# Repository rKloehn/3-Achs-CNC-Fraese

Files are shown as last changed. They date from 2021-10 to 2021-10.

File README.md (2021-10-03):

# 3-Achs-CNC-Fraese

Selfmade CNC-Mill for Aluminum, Wood and Steel milling

## Overview
To mill wood, aluminum and steel for future project, the desicion was made to design, construct a DIY-CNC mill. The basic concept is based upon an typical portal style cnc-mill, which is quite common in the diy world. To better stabilise and actualy mill aluminum and steel, the cnc is made out of steel beams. The mill has an work area of X500, Y700, Z150 milimeters. To drive the axis three iHSV57 servomotors with 180W each are used. The axes are guided by linear guides and driven by three ball screws. At the end of each axis there is a limit switch that can detect the end position. To control the axis, a MESA 7i76E is used, which is connected to an Intel NUC with an Ethernet cable. All three motors have a 36V power supply with max. 8.9 Ampere. The MESA card is operated with a 24V power supply. The control is done by Linux CNC.

## Work Progress
## 1. Create CAD Model 
A CAD model was created in Solidworks. Here, different concepts were first considered. In the end, I decided in favor of the steel body construction.
<p align="center">
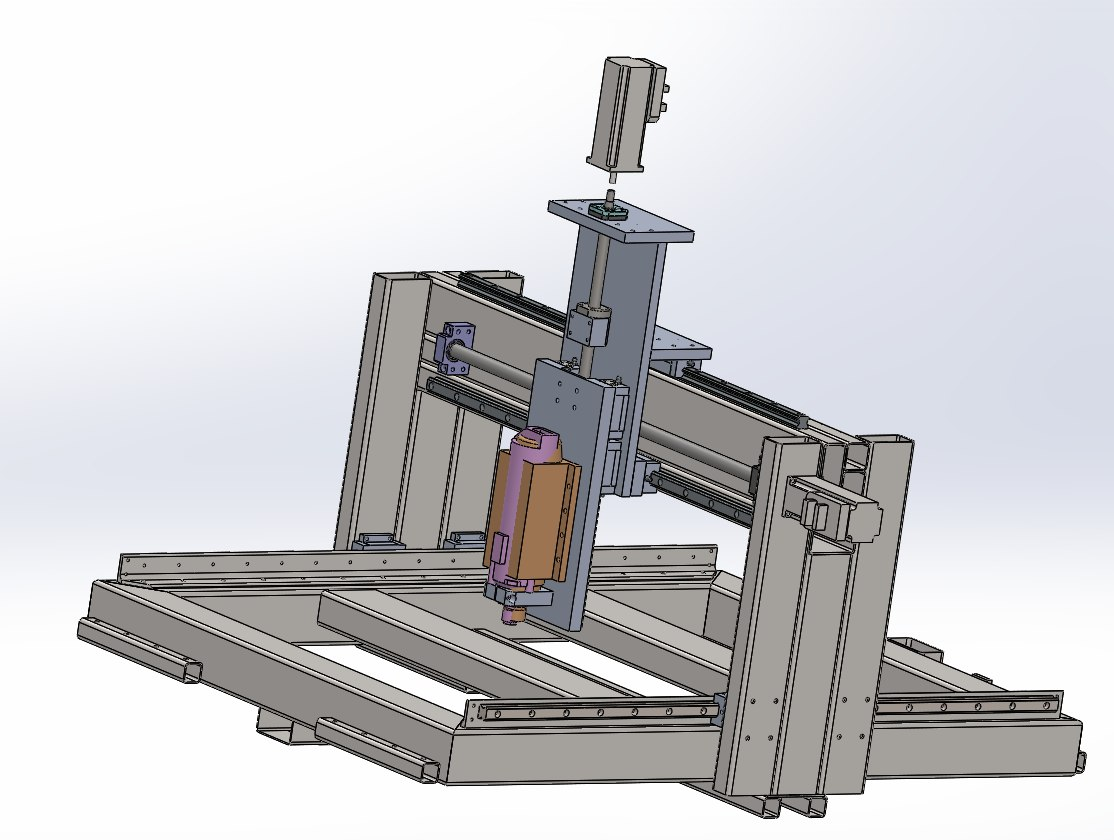
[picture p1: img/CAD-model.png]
	
</p>

## 2. Weld and prime base frame 
The base frame was made of 80x80x3 square steel tubes. The cross braces are 100x50x3 square steel tubes. All tubes are welded together without much distortion as possible. After that the frame is sleeved for priming and then primed
<p align="center">
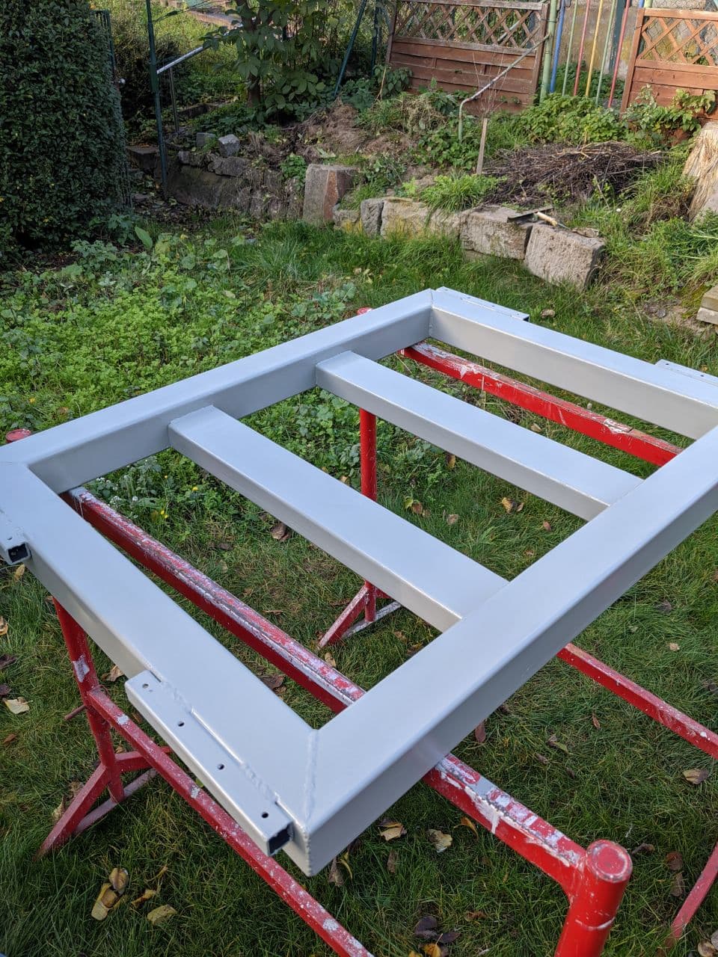
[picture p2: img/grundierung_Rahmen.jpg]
	
</p>

## 3. Manufacture portal
The portal is not welded because the risk of something warping during welding is too great. Gluing was used as an alternative to welding. The gantry was also bolted to support the adhesive bond. For the gluing process, a wooden jig was built so that the portal can be glued perfectly square and in the correct position. The portal was also primed and painted.
<p align="center">
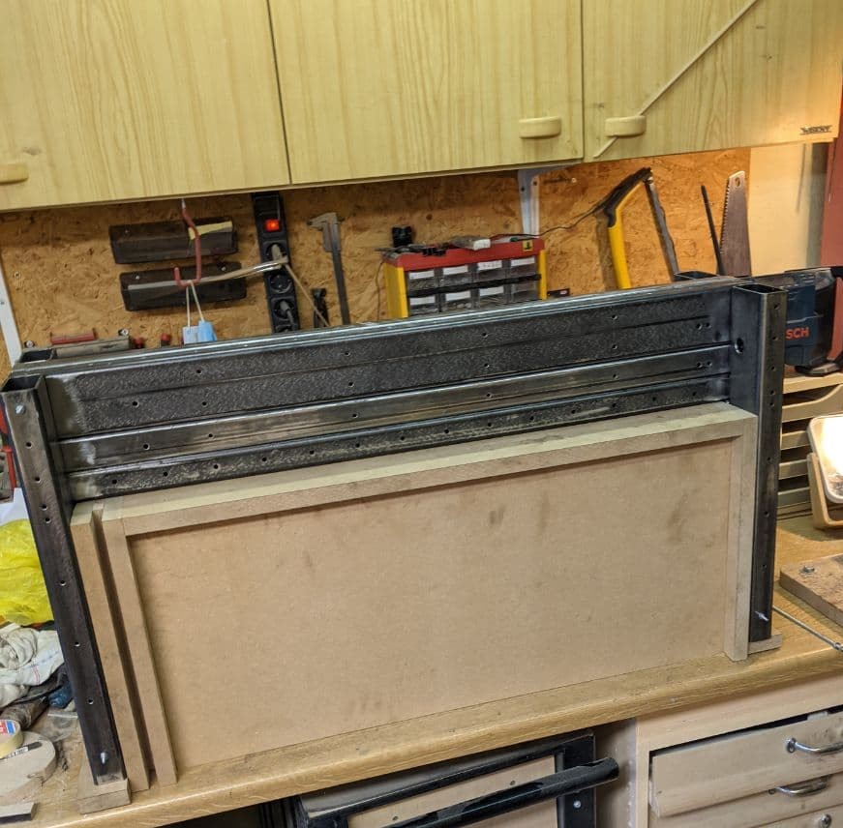
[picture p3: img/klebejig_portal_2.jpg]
	
</p>

## 4.First assembly
First assembly without fixed connection to detect errors in welding or bonding at an early stage.
<p align="center">
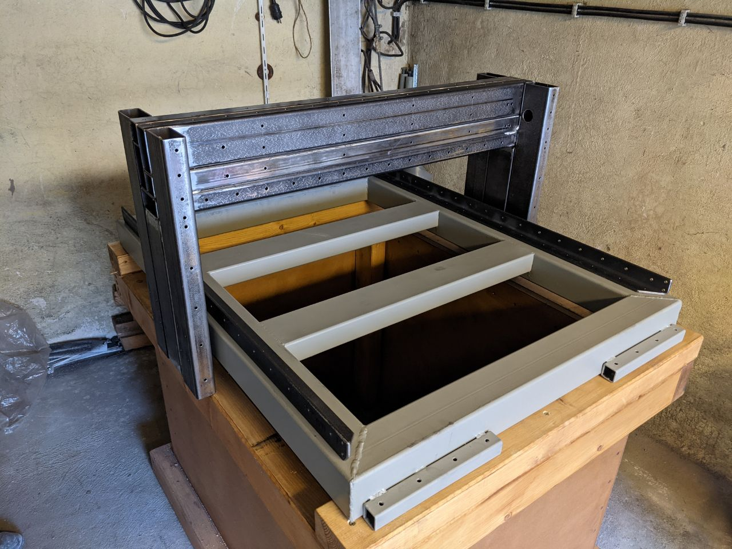
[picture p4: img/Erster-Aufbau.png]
	
</p>

## 5. Mounting of all spindles and linear guides
Finishing the painting and mounting the ball screw and carriages on the linear guides. Initially, only the y-axis was mounted on which the gantry is fixed. After the portal runs smoothly, the spindle and x-axis were mounted. 
<p align="center">
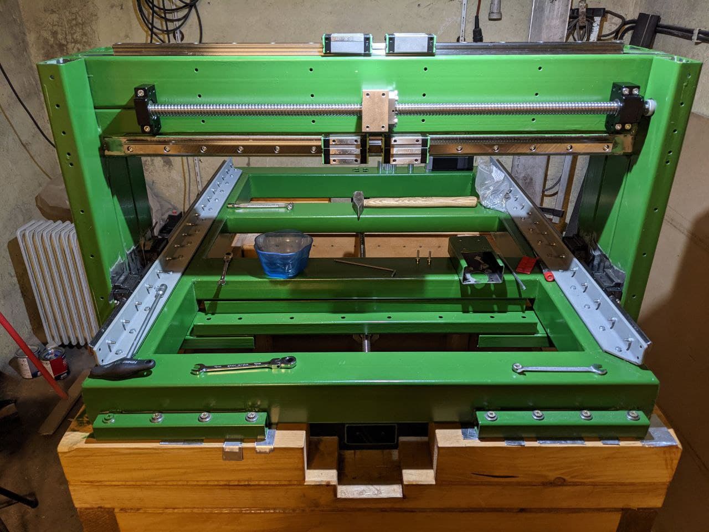
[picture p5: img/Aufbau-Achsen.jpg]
	
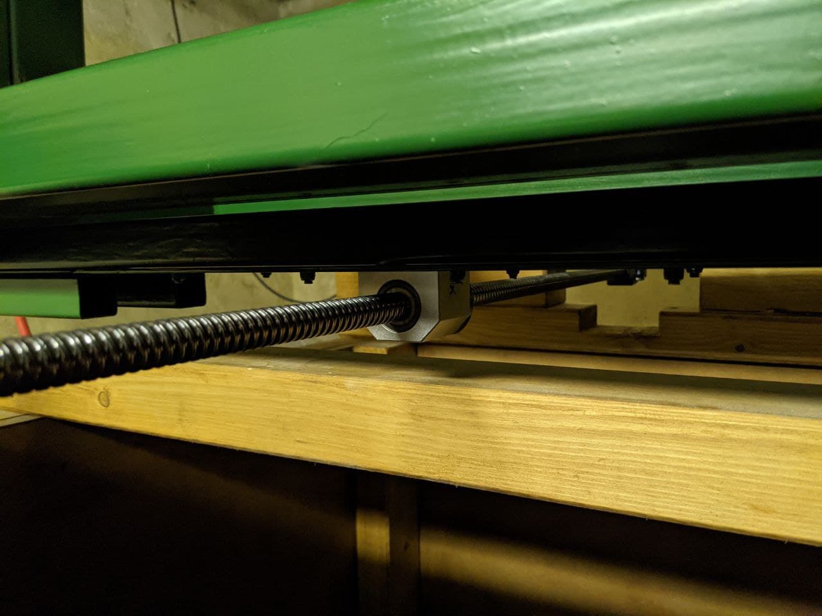
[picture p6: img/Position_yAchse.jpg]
	
</p>

## 6. Control cabinet 
Placement and wiring of all electronic components in the control cabinet.
<p align="center">
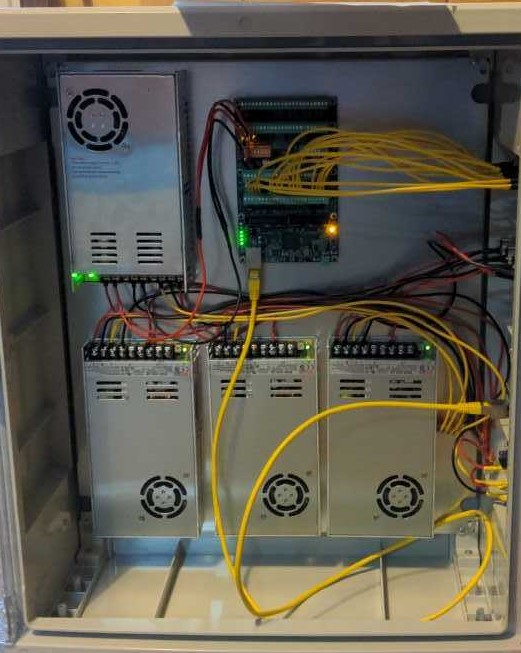
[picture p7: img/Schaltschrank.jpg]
	
</p>

## 7. Aligning the x-axis and y-axis and mounting z-axis
The x- and y-axes are aligned with each other and the z-axis was mounted to the carriage of the x-axis. The z-axis is also aligned perpendicular to the x-axis
<p align="center">
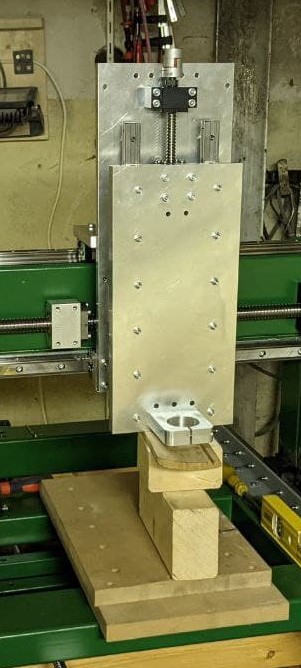
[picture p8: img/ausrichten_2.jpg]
	
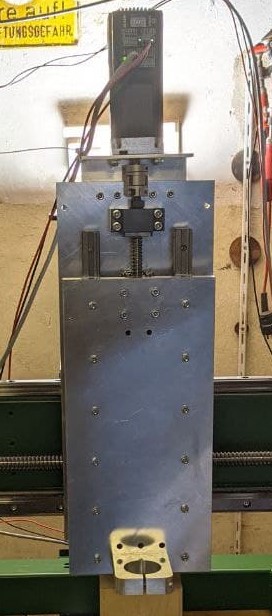
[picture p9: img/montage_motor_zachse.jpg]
	
</p>

## 8. Connecting the motors and first test run
Motors are connected to the control cabinet using XCT connectors. Limit switches are attached and connected to the axes and by checking the motor current it is determined whether the axes are all running smoothly.
<p align="center">
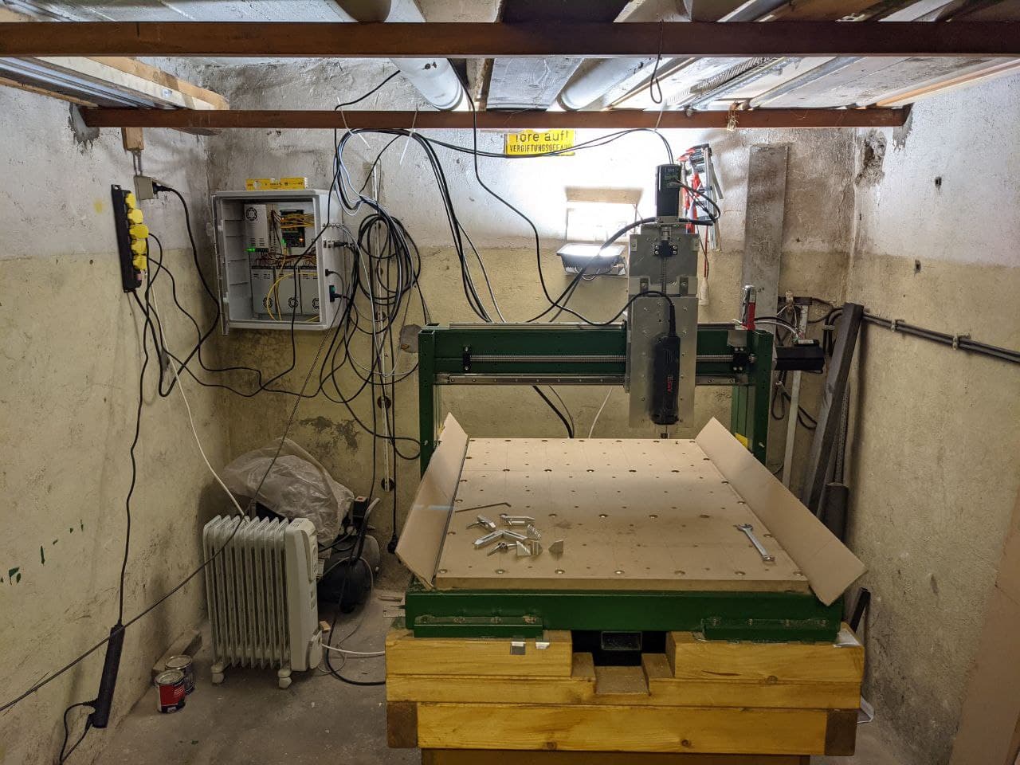
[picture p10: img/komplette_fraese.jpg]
	
</p>

## 9. First aluminum test part
As a first test component, two key fobs were designed in CAD and the milling program was programmed using HSMWorks. A 4mm end mill and a 45° engraving cutter were used for the part. As a first test component, two key fobs were designed in CAD and the milling program was programmed using HSMWorks. A 4mm end mill and a 45° engraving cutter were used for the part. The keychain is a game character from a video game.

<p align="center">
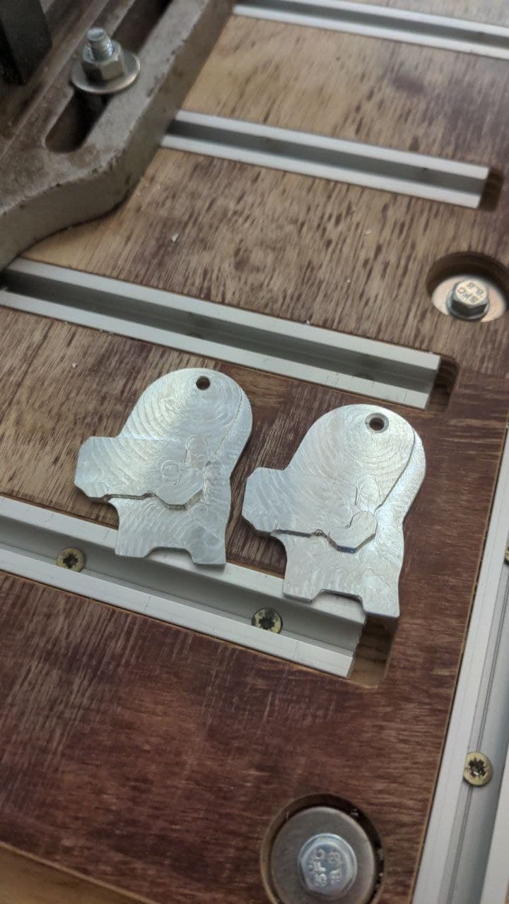
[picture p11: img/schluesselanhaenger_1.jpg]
	
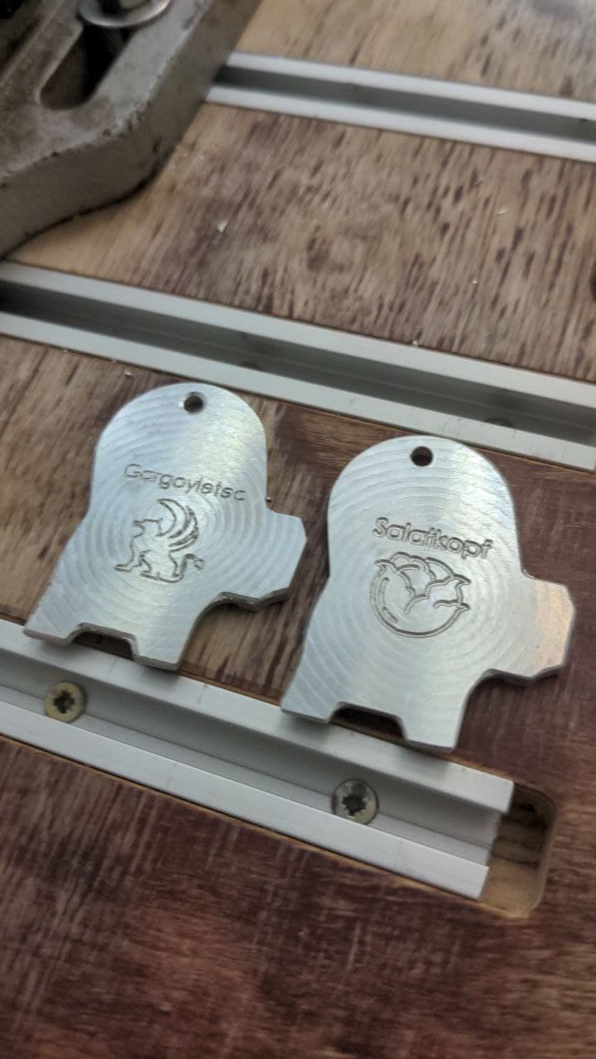
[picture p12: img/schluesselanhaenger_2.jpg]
	
</p>

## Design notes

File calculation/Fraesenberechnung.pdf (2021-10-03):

Nm N m :=

## CNC Fräse Auslegung:

notwendige Daten:
Eilganggeschwindigkeit: | v
e

3.6

m
min

0.06

m
s
:= | = |
Dauer der Beschleunigungsrampe: | t
r

:= 0.2s

Gewicht des Portals: | mportal := 65kg
Schätzwert Schnittkraft: | FSchnitt := 100N
Reibungszahl der Führungen: | ρFührung := 0.02
Wirkungsgrad Spindel: | ηSpindel := 0.3
Länge der Spindel: | lSpindel := 1000mm
Durchmesser der Spindel: | dSpindel := 20mm
Spindelsteigung: | xSpindel := 5mm
Getriebeübersetzung: | iG

:= 1

Trägheitsmoment Motor: | JM | 290gm cm2
:= |
Dichte Spindel: | φSpindel | 7.83

gm

cm

3

:=

s

sicherheit := 2 Sicherheitsfaktor:

Berechnung Geschwindigkeiten:

Motor:

Drehzahl des Motors bei Eilgang: | n
e

v
e
x( | ) Spindel

720

1
min
:= | = |
Winkelgeschwindigkeit der Motors bei Eilgang: | ωe

2π n
e
- 75.398

1
s
:= | =
Winkelbeschleunigung innerhalb der Rampe: | αe

ωe
t
r

376.991

1

s

2

:= =

Spindel:

Drehzahl der Spindel bei Eilgang: | n
s

n
e

iG

- 720

1
min
:= | = |

ωs

2π n
s
- 75.398

1
s
:= | = Winkelgeschwindigkeit der Spindel bei Eilgang:

αs

ωs
t
r

376.991

1

s

2

:= = Winkelbeschleunigung innerhalb der Rampe:

Drehmomentberechnung:

Reibungskraft Tisch/Portal: | Fr
9.81

m

s

2

mportal | ρFührung := | | = 12.753 N

Fr

:= 20N
Reibmoment an der Motorwelle: | TRM

Fr

xSpindel

### 6.28 ηSpindel

:= | = 0.053 Nm
Schnittmoment an der Motorwelle: | TSchnitt

FSchnitt xSpindel

### 6.28 ηSpindel

:= | = 0.265 Nm
Masse Spindel: | mSpindel | φSpindel lSpindel | π

dSpindel

2

4

:= | | = 2.46 kg
Trägheitsmoment Spindel: | JSpindel | 0.5 mSpindel

dSpindel
2

2
- 1.23 kg cm2
:= | = |
Trägheitsmoment Tisch/Portal: | JPortal | mportal

xSpindel
6.28

2
- 4.12 10- 5
- m

2
:= | = | kg

Drehmoment statische Last: | Tstatisch

TRM TSchnitt +

iG

| := | | | = 0.318 Nm
Drehmoment dynamsiche Last: | Tdynamisch | JPortal JSpindel ( | ) + | αs
:= | = 0.062 Nm
TBeschl | JM αe
- | Tdynamisch := | + | = 0.073 Nm Drehmoment zur Beschleunigung des Motors:
Erforderliches Drehmoment: | TGesamt | Tstatisch Tdynamisch + | TBeschl := | + | = 0.453 Nm
Drehmoment mit Sicherheit: | TSicherheit | TGesamt s
sicherheit := | | = 0.906 Nm

## Berechnung für das Kleben des Portalträgers

Gramm kg 10- 3
:=
VKlebe 15000mm3

### 15 cm3

:= | =

TH

:= 120
ρHärter 0.96

Gramm

cm

3

:=

TB

:= 100
ρBinder 1.2

Gramm

cm

3

:=

Volumenteile Härter:

VH

TH

1
ρHärter

Gramm

cm

3

:= | | = 125

Volumenteile Binder:

VB

TB

1
ρBinder

Gramm

cm

3

:= | | = 83.333

Mischungsverhältnis für Volumen:

VMischung

VH
VB

:= 100 = 150

VHärter

VKlebe

1

100
150

+

### 9 cm3

:= | =
VBinder | VKlebe VHärter - | 6 cm3
:= | =
mHärter | VHärter ρHärter := | | = 8.64 Gramm
mBinder | VBinder ρBinder := | | = 7.2 Gramm

mHärter
mBinder

= 1.2

bPortal := 950mm

Tmax := 40K 274.15K + | = 314.15 K
Tmin := -10K 274.15K + | = 264.15 K
TRaum := 20K 274.15K + | = 294.15 K

ΔT

Tmax T ( | ) - Raum
Tmin T ( | ) - Raum

20
-30
:= | = | K
St37 | 11.1 10- 6

1
K

:=

Alu5083 24.2 10- 6

1
K

2.42 10- 5

1
K
:= | =
Δα Alu5083 St37 - | 1.31 10- 5

1
K
:= | =
Δl20 | bPortalΔα ΔT
0
:= | | = 0.249 mm
Δl30 | bPortalΔα ΔT
1
:= | | = -0.373mm
Δl T( ) | b := PortalΔαT
T := -40K 39 , - K.. 30K
ΔlStahl( ) | b T | Portal := | St37T
ΔlAlu( ) | b T | Portal := | Alu5083T
pulse_rev | 3200 :=
spindel_steigung | 4 :=
pulse_rev | 1
spindel_steigung
- = 800

## Längenausdehnung

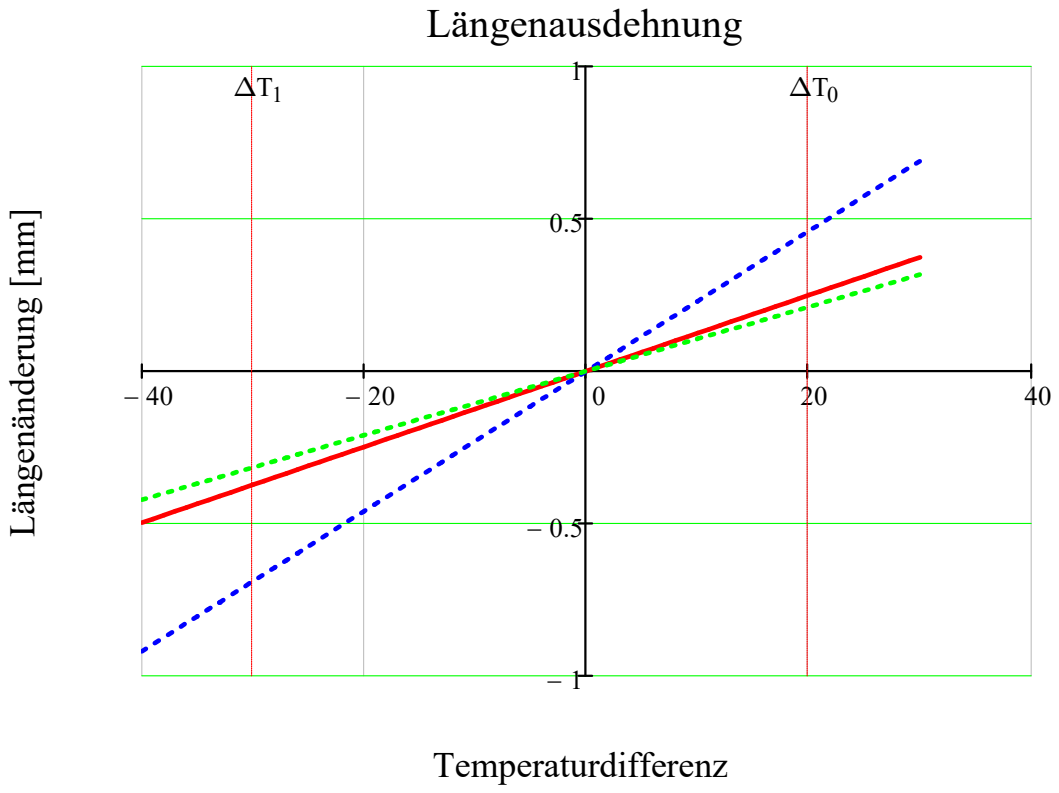
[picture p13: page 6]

ΔT1 | Temperaturdifferenz Längenänderung [mm]

A - 23 | A -20

LA

:= 620mm | LA20 := 540mm

b

23 := 12mm | b 20 := 12mm

h

23 := 8mm | h 20 := 8mm

dA

LA
π
:= | = 197.352 mm | dA20

LA20
π

:= = 171.887 mm

d
i

dA

2 h23 := | - ( ) = 181.352 mm | d
i20 | dA20 | 2 h20 := | - ( ) = 155.887 mm

LI

d
i
:= π = 569.735 mm | LI20 | d
i20 := | π = 489.735 mm

AG

108m2
:=

AR

2.7m 4.6 m 12.42m2
:= | =
A1 | 4.8m 3.5 m 16.8 m2
:= | =
A2 | 4m 4 m 16 m2
:= | =
Ap | AG AR
- A1
- A2
- 62.78 m2
:= | =

P

AR
Ap
:= | = 0.198
Preis | 1183.5 :=
Total | P 1183.5 := | = 234.136

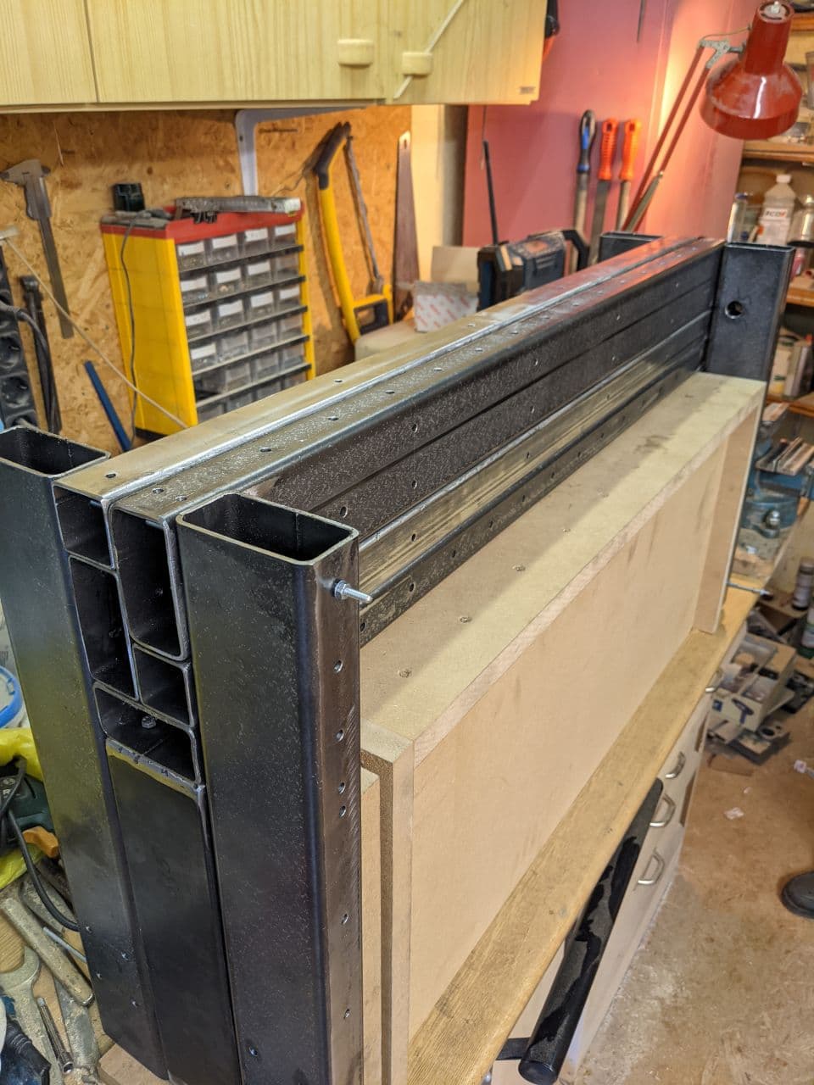
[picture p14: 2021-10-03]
img/klebejig_portal_1.jpg

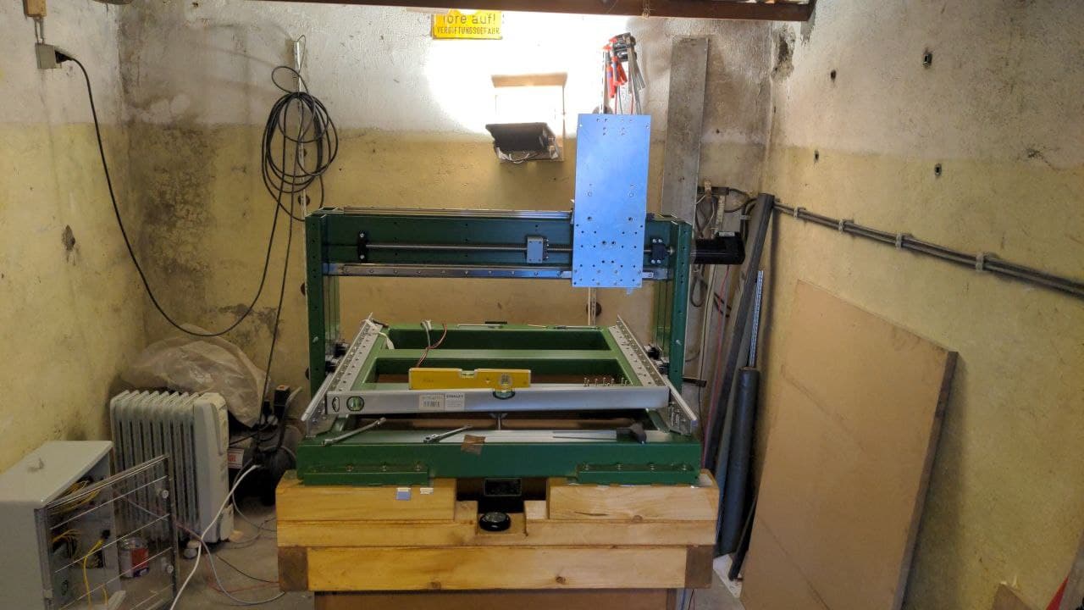
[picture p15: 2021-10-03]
img/ausrichten.jpg

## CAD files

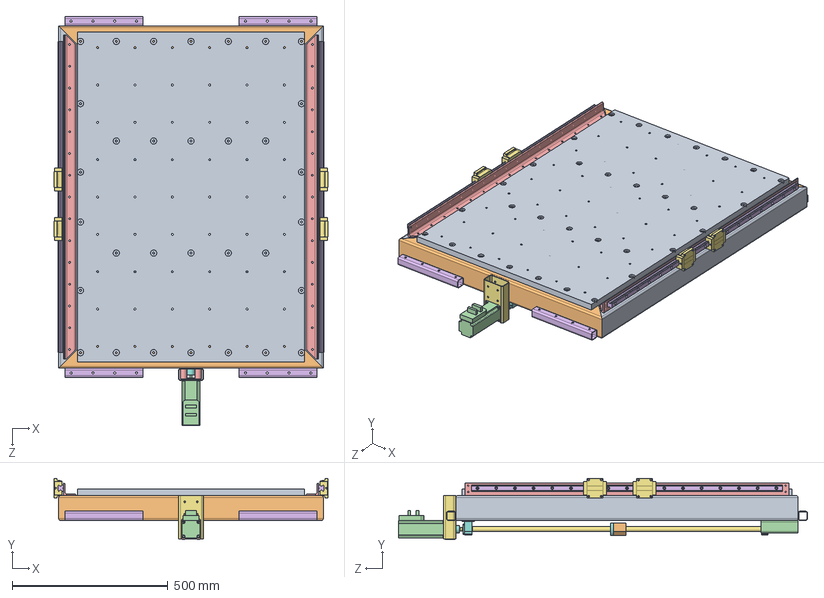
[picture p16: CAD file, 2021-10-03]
cad/Rahmen/Rahmen-St - Tisch Grund zus.SLDASM
880.0 x 197.0 x 1314.0 mm
Rahmen-St - Tisch - Längsrohr x 2
Rahmen-St - Tisch - Querrohr x 2
Rahmen-St - Tisch - Brett-Rohr x 2
Sorotec-iHSV57-30-18-36-21-38
Rahmen-St - Tisch - Motor-Buchse x 4
Profilfuehrung20x1000 x 2
Profil-Flansch-wagen 20er - CR-2016a x 4
F6rper.stp
Rolling bearing 7001 C GB_T 292-94.stp
Rolling bearing 7001 AC GB_T 292-94.stp
BK12-Distanzring.stp
BK12-Abdeckkappe.stp
BK12-Dinstanzring-vorne.stp
BK12-Dinstanzring-hinten.stp
KUS1605x1000
Spindelmutter-1605
Steh-Loslager neu KUS16
Spannblock KUS16
Rahmen-St - Auflage Rahmen 1
Rahmen-St - Tisch - Spindel Lager 2
Rahmen-St - Winkel Führung x 2
Rahmen-St - Tisch - Anschraub-Rohr x 4
Rahmen-St - Tisch - Motor Lager
WK25-8auf10
Tisch - Tischplatte mit Gewinde

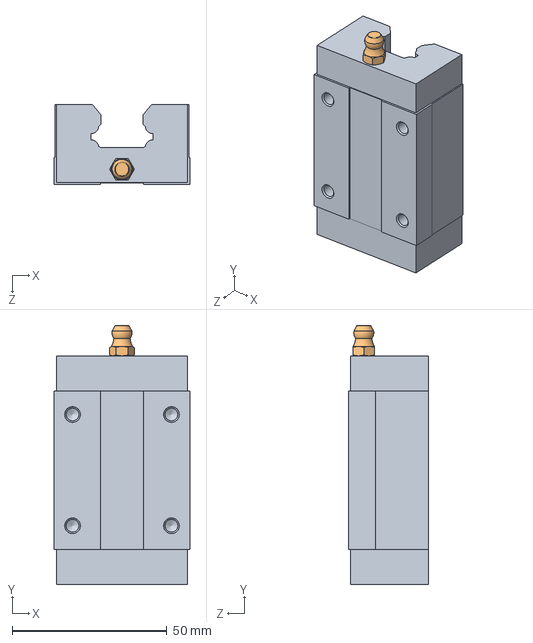
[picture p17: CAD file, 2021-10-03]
cad/Normteile/Profilwagen 20er - CR-2016a mit Nippel.SLDASM
44.0 x 83.8 x 26.0 mm
Profilwagen 20er - CR-2016a
Nippel für 20er

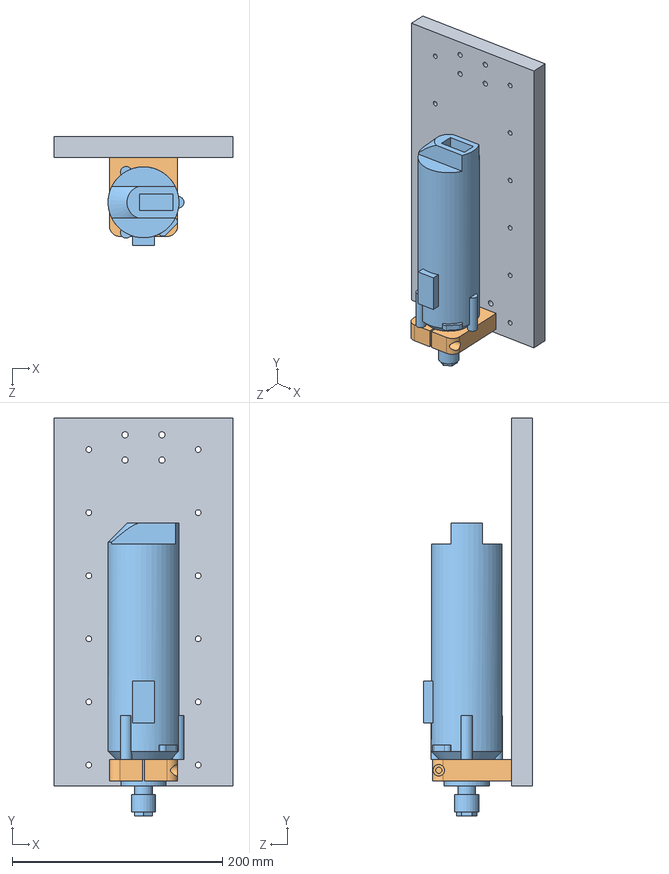
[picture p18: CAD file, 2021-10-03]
cad/zAchse/Z - Achse - Zus.SLDASM
170.0 x 378.5 x 103.5 mm
Z-Achse - Platte
Eurohalsaufnahme 43
Spindelmotor 1050 FME-1

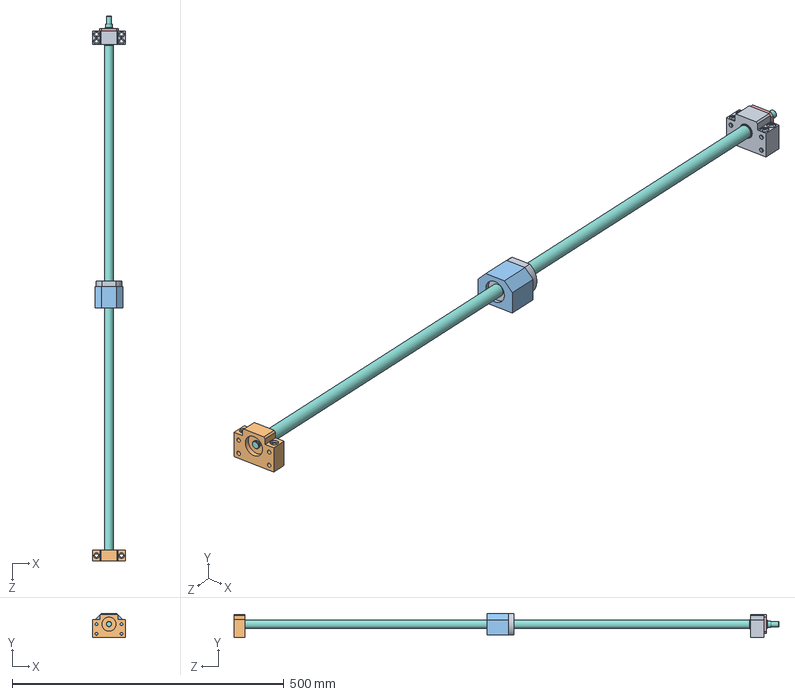
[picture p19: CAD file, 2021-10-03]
cad/Rahmen/Rahmen-St - Kugelspindel 16x900-re.SLDASM
60.0 x 45.0 x 1003.0 mm
F6rper.stp
Rolling bearing 7001 C GB_T 292-94.stp
Rolling bearing 7001 AC GB_T 292-94.stp
BK12-Distanzring.stp
BK12-Abdeckkappe.stp
BK12-Dinstanzring-vorne.stp
BK12-Dinstanzring-hinten.stp
KUS1605x1000
Spindelmutter-1605
Steh-Loslager neu KUS16
Spannblock KUS16

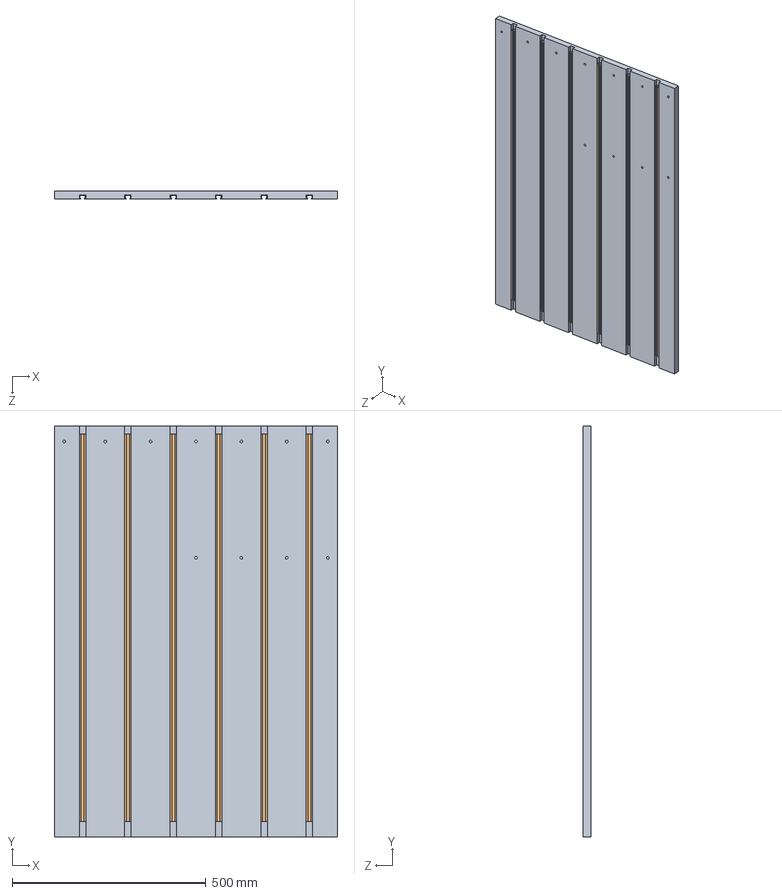
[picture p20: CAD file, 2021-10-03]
cad/Tisch/Tisch - Tischplatte Zus.SLDASM
730.0 x 1060.0 x 21.0 mm
Tisch - Tischplatte mit Nuten
C-Profil 8 - 1000mm x 6

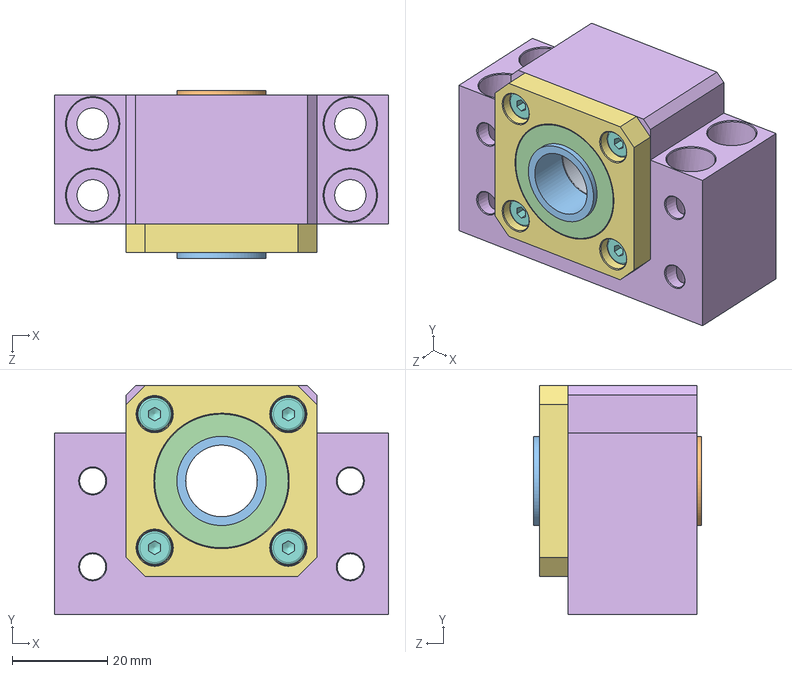
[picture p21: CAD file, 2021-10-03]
cad/Normteile/Steh-Festlager KUS20-20171205.SLDASM
70.0 x 48.0 x 35.3 mm
inafag_b7002-c-t-p4s_5mktdp0cwb119am4yeiejssnx_01.stp x 2
inafag_b7002-c-t-p4s_5mktdp0cwb119am4yeiejssnx_02.stp x 2
inafag_b7002-c-t-p4s_5mktdp0cwb119am4yeiejssnx_03.stp x 2
inafag_b7002-c-t-p4s_5mktdp0cwb119am4yeiejssnx_04.stp x 2
inafag_b7002-c-t-p4s_5mktdp0cwb119am4yeiejssnx_05.stp x 2
inafag_b7002-c-t-p4s_5mktdp0cwb119am4yeiejssnx_06.stp x 2
inafag_b7002-c-t-p4s_5mktdp0cwb119am4yeiejssnx_07.stp x 2
inafag_b7002-c-t-p4s_5mktdp0cwb119am4yeiejssnx_08.stp x 2
inafag_b7002-c-t-p4s_5mktdp0cwb119am4yeiejssnx_09.stp x 2
inafag_b7002-c-t-p4s_5mktdp0cwb119am4yeiejssnx_10.stp x 2
inafag_b7002-c-t-p4s_5mktdp0cwb119am4yeiejssnx_11.stp x 2
inafag_b7002-c-t-p4s_5mktdp0cwb119am4yeiejssnx_12.stp x 2
inafag_b7002-c-t-p4s_5mktdp0cwb119am4yeiejssnx_13.stp x 2
Festlager.stp
Abdeckkappe.stp
DIN 7984 - M4 x 6.stp x 4
Distanzring.stp
BK15-Dinstanzring-hinten.stp
BK15-Dinstanzring-vorne.stp
Wellendichtring.stp x 2

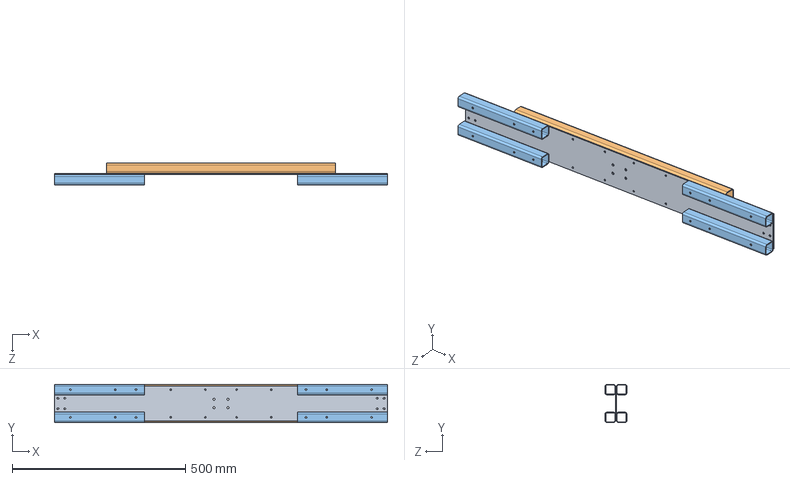
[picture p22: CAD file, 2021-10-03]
cad/Portal/Portal - Schieber - Zus.SLDASM
960.0 x 110.0 x 63.0 mm
Portal - Schieber-Blech
Portal - Schieber-Rohr x 2
Portal - Schieber-Rohr-unten x 4

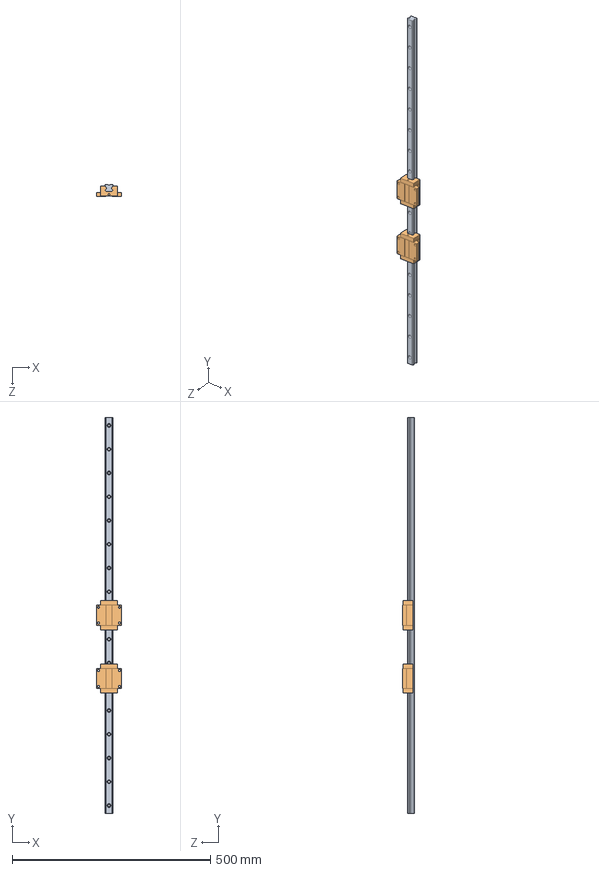
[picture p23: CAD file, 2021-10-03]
cad/Rahmen/Rahmen-St - Profilführung 20er-1000.SLDASM
63.0 x 1000.0 x 30.0 mm
Profilfuehrung20x1000
Profil-Flansch-wagen 20er - CR-2016a x 2

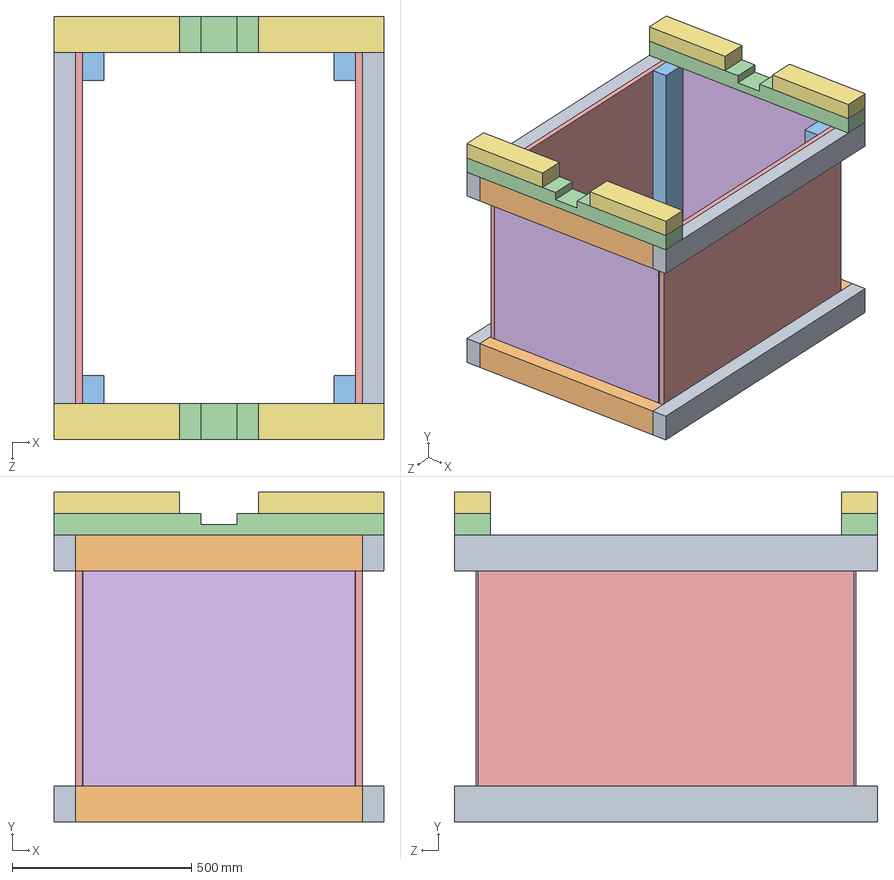
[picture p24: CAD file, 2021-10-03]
cad/Tisch/Tisch - ZusSt-Alu.SLDASM
920.0 x 920.0 x 1180.0 mm
Tisch - längsSt-Alu x 4
Tisch - querSt-Alu x 4
Tisch - BeinSt-Alu x 4
Tisch - AuflageSt-Alu x 2
Tisch - Wand - längsSt-Alu x 2
Tisch - Wand - querSt-Alu x 2
Tisch - Anschrauben-Auflage x 4

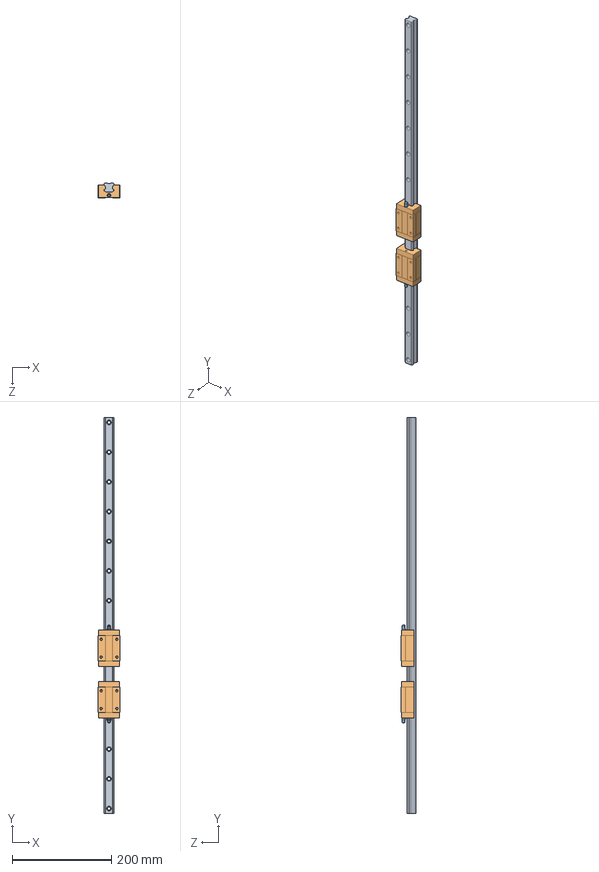
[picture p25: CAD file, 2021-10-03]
cad/Portal/Portal - Linearführung 800.SLDASM
44.0 x 800.0 x 30.0 mm
Profilführung 20er - 800 lg
Profilwagen 20er - CR-2016a x 2
Nippel für 20er x 2

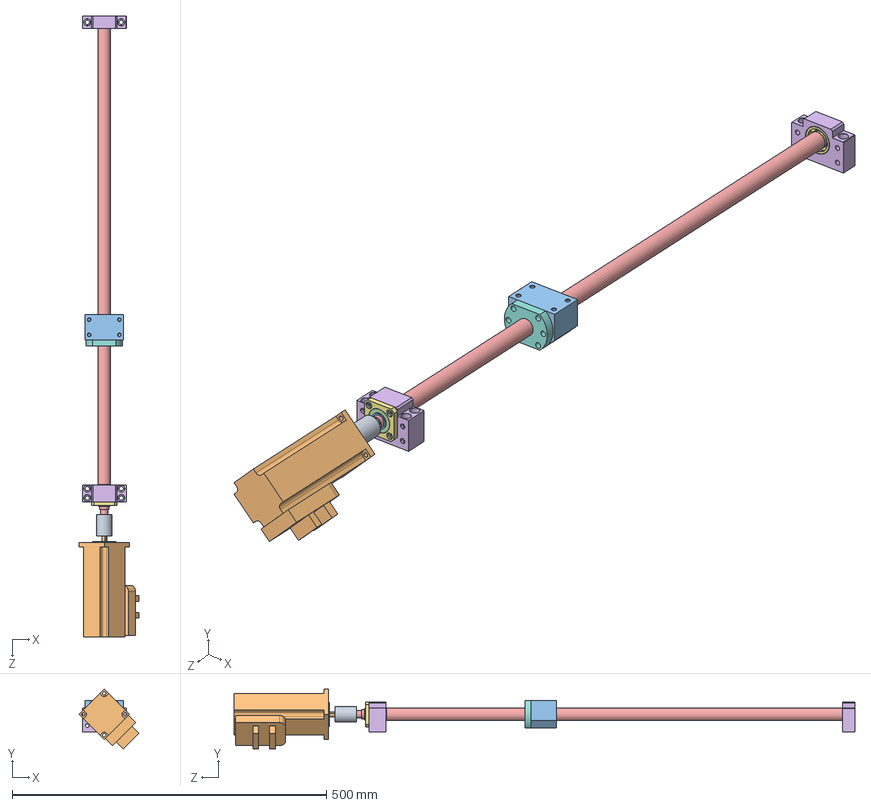
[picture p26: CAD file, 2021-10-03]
cad/Portal/Portal - Spindel 20x800.SLDASM
95.7 x 95.5 x 988.0 mm
inafag_b7002-c-t-p4s_5mktdp0cwb119am4yeiejssnx_01.stp x 2
inafag_b7002-c-t-p4s_5mktdp0cwb119am4yeiejssnx_02.stp x 2
inafag_b7002-c-t-p4s_5mktdp0cwb119am4yeiejssnx_03.stp x 2
inafag_b7002-c-t-p4s_5mktdp0cwb119am4yeiejssnx_04.stp x 2
inafag_b7002-c-t-p4s_5mktdp0cwb119am4yeiejssnx_05.stp x 2
inafag_b7002-c-t-p4s_5mktdp0cwb119am4yeiejssnx_06.stp x 2
inafag_b7002-c-t-p4s_5mktdp0cwb119am4yeiejssnx_07.stp x 2
inafag_b7002-c-t-p4s_5mktdp0cwb119am4yeiejssnx_08.stp x 2
inafag_b7002-c-t-p4s_5mktdp0cwb119am4yeiejssnx_09.stp x 2
inafag_b7002-c-t-p4s_5mktdp0cwb119am4yeiejssnx_10.stp x 2
inafag_b7002-c-t-p4s_5mktdp0cwb119am4yeiejssnx_11.stp x 2
inafag_b7002-c-t-p4s_5mktdp0cwb119am4yeiejssnx_12.stp x 2
inafag_b7002-c-t-p4s_5mktdp0cwb119am4yeiejssnx_13.stp x 2
Festlager.stp
Abdeckkappe.stp
DIN 7984 - M4 x 6.stp x 4
Distanzring.stp
BK15-Dinstanzring-hinten.stp
BK15-Dinstanzring-vorne.stp
Wellendichtring.stp x 2
KUS2005x800
Loslager.stp
DIN 625 SKF - SKF 6002.stp
KUS2005 Spindelmutter
WK25-8auf12
Sorotec-iHSV57-30-18-36-21-38
Spannblock KUS20

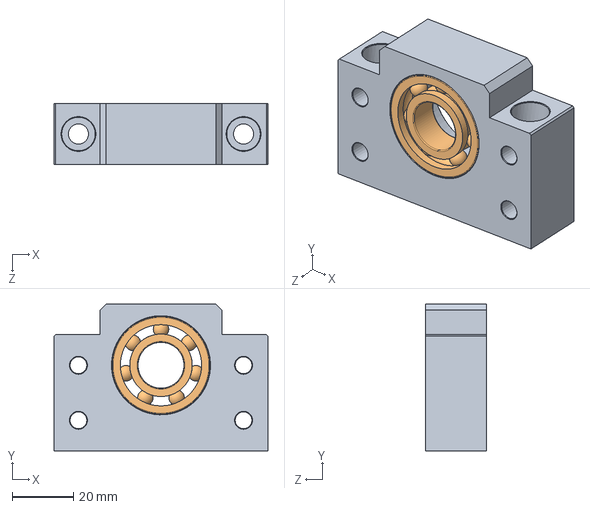
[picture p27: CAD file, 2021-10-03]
cad/Normteile/Steh-Loslager KUS2020150511.SLDASM
70.0 x 48.0 x 20.0 mm
Loslager.stp
DIN 625 SKF - SKF 6002.stp

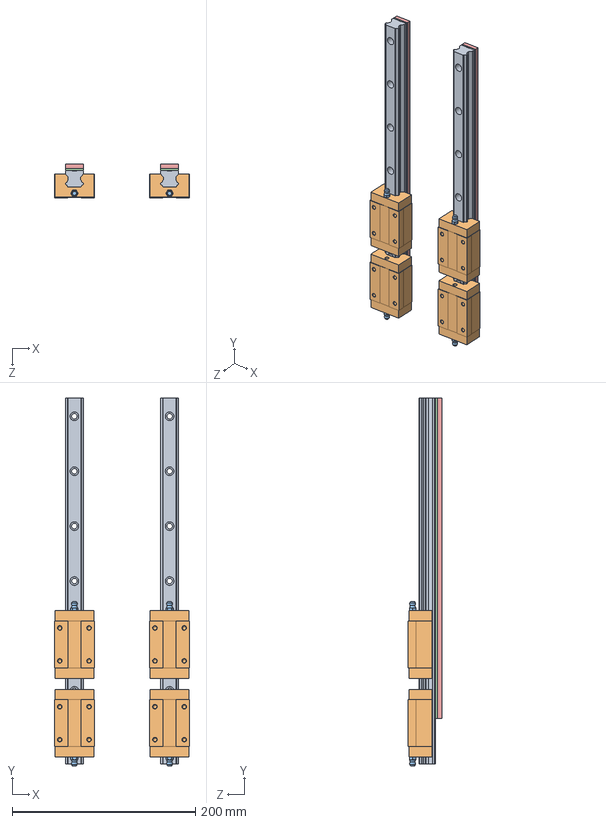
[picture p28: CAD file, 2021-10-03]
cad/Portal/Portal - Z -Profilführung 20er 400.SLDASM
148.0 x 402.1 x 37.0 mm
Profilfuehrung20x400 x 2
Profilwagen 20er - CR-2016a x 4
Nippel für 20er x 4
Portal - Flach unter Schiene x 2
Portal - Flach 5 unter Schiene x 2

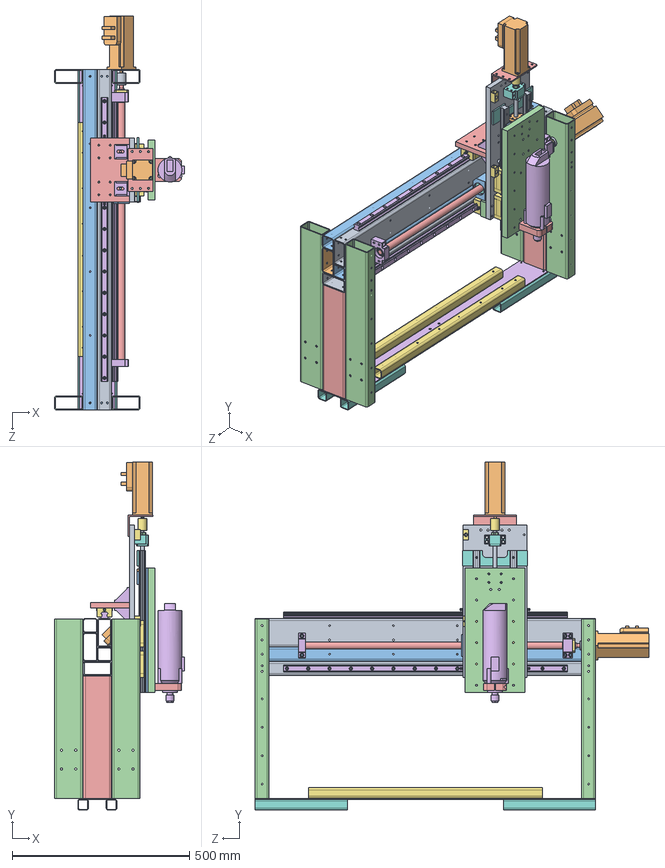
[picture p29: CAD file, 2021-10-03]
cad/Portal/Portal - Zus-St2.SLDASM
366.5 x 980.5 x 1110.0 mm
Portal - quer Rechteckrohr 80x40x3 x 2
Portal - quer Rechteckrohr 80x40x2
Portal - quer Rechteckrohr 40x40x2 x 2
Portal - Wange1 Rechteckrohr 80x40x3 x 4
Portal - Wange2 Rechteckrohr 80x40x2 x 2
Profilführung 20er - 800 lg x 2
Profilwagen 20er - CR-2016a x 8
Nippel für 20er x 8
inafag_b7002-c-t-p4s_5mktdp0cwb119am4yeiejssnx_01.stp x 2
inafag_b7002-c-t-p4s_5mktdp0cwb119am4yeiejssnx_02.stp x 2
inafag_b7002-c-t-p4s_5mktdp0cwb119am4yeiejssnx_03.stp x 2
inafag_b7002-c-t-p4s_5mktdp0cwb119am4yeiejssnx_04.stp x 2
inafag_b7002-c-t-p4s_5mktdp0cwb119am4yeiejssnx_05.stp x 2
inafag_b7002-c-t-p4s_5mktdp0cwb119am4yeiejssnx_06.stp x 2
inafag_b7002-c-t-p4s_5mktdp0cwb119am4yeiejssnx_07.stp x 2
inafag_b7002-c-t-p4s_5mktdp0cwb119am4yeiejssnx_08.stp x 2
inafag_b7002-c-t-p4s_5mktdp0cwb119am4yeiejssnx_09.stp x 2
inafag_b7002-c-t-p4s_5mktdp0cwb119am4yeiejssnx_10.stp x 2
inafag_b7002-c-t-p4s_5mktdp0cwb119am4yeiejssnx_11.stp x 2
inafag_b7002-c-t-p4s_5mktdp0cwb119am4yeiejssnx_12.stp x 2
inafag_b7002-c-t-p4s_5mktdp0cwb119am4yeiejssnx_13.stp x 2
Festlager.stp
Abdeckkappe.stp
DIN 7984 - M4 x 6.stp x 4
Distanzring.stp
BK15-Dinstanzring-hinten.stp
BK15-Dinstanzring-vorne.stp
Wellendichtring.stp x 2
KUS2005x800
Loslager.stp
DIN 625 SKF - SKF 6002.stp
KUS2005 Spindelmutter
WK25-8auf12
Sorotec-iHSV57-30-18-36-21-38 x 2
Spannblock KUS20
Portal - Wagen-Distanz-Platte
Portal - Oberplatte
Portal - Schieber-Blech
Portal - Schieber-Rohr x 2
Portal - Schieber-Rohr-unten x 4
Profilfuehrung20x400 x 2
Portal - Flach unter Schiene x 2
Portal - Flach 5 unter Schiene x 2
Z-Achse - Platte
Eurohalsaufnahme 43
Spindelmotor 1050 FME-1
WK25-8auf8
Steh-Festlager neu KUS12
KUS1204x400
Spindelmutter-KUS1204
Spannblock KUS12
KUS1204 Fest-Mutter
Z - Achse - Motor-Halter
Winkel 45x45 x 4
Z - Achse - Anschlag Fuss 1 x 2
Z - Achse - Anschlag Flach 1
Portal - Frontplatte

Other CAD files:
cad/Normteile/Kugelspindel 12x400 - ein Festlager.SLDASM
cad/Normteile/Steh-Festlager KUS16-20150517.SLDASM
cad/Normteile/Nippel für 20er.SLDPRT
cad/Portal/Portal - Oberplatte.SLDPRT
cad/Normteile/C-Profil 8 - 1000mm.SLDPRT
cad/Normteile/China Spindel 2,2 KW Luftgekühlt.SLDPRT
cad/Normteile/Flansch-Festlager KUS16-20160127.stp
cad/Normteile/KUS1204 Fest-Mutter.SLDPRT
cad/Normteile/KUS1204x400.SLDPRT
cad/Normteile/KUS1204x400.stp
cad/Normteile/KUS1605x1000.SLDPRT
cad/Normteile/KUS1605x1000.stp
cad/Normteile/KUS2005 Spindelmutter.SLDPRT
cad/Normteile/KUS2005 Spindelmutter.stp
cad/Normteile/KUS2005x800.SLDPRT
cad/Normteile/Profilfuehrung20x1000.SLDPRT
cad/Normteile/Profilfuehrung20x1000.stp
cad/Normteile/Profilfuehrung20x400.SLDPRT
cad/Normteile/Profilfuehrung20x500.stp
cad/Normteile/Profilführung 20er - 800 lg.SLDPRT
cad/Normteile/Profilwagen 20er - CR-2016a.SLDPRT
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

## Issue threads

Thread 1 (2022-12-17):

Big fan

m-tosch, 2022-12-17:
I don't have an issue with this project

Just wanted to say that i love the enormous effort and passion being displayed here 💯

You are a true master of your craft 🔨

May you live long and prosper 🖖

Thank you for serving humanity 🙏

- Anonymous fan
